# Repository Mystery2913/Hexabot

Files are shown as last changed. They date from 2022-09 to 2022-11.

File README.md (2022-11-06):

# Hexabot - A hexapedal robot from scratch


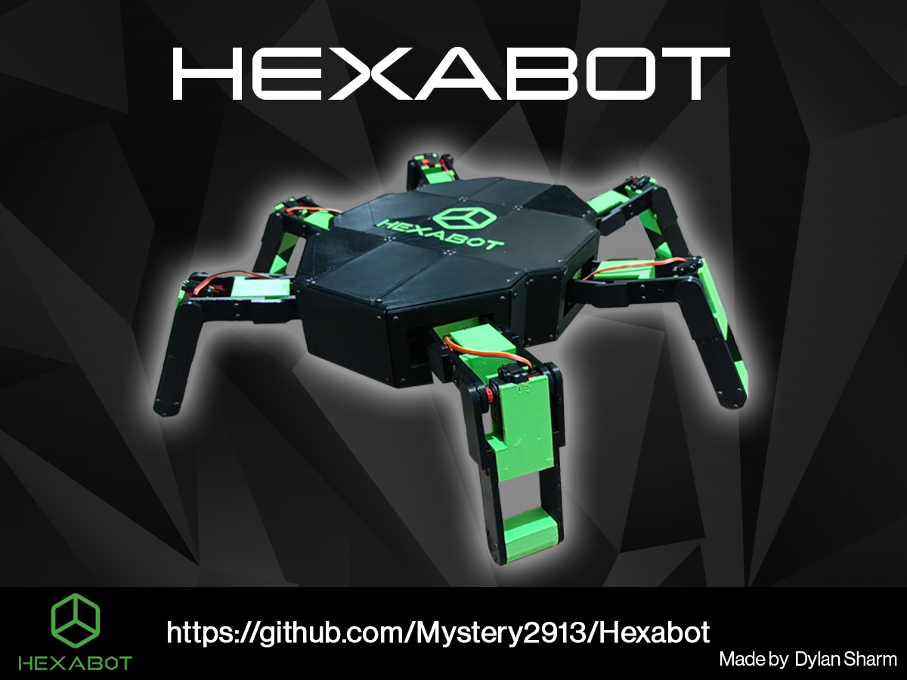
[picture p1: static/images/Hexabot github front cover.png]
Front Cover Image of Hexabot


## Introduction
Author: **Dylan Sharm**

**Hexabot** is a fully developed hexapedal robot made using 3D printing. Comprising of a 3D printed body, it contains the leg mechanisms for 3 joints to move each leg in 3 dimensions. All 6 legs allow for a stable base for walking around. The system is controlled by a local website run on a Raspberry Pi 4, while control system features speed control and standing control. The robot is powered by a 7.4v 7500mAh battery that is removable from the robot with power indicator light included.

## Building Hexabot
To build Hexabot, follow the **[user manual](Hexabot_User_Manual.pdf)**. It details all instructions of how to make Hexabot including components and tools, materials, assembly instructions and diagrams, software instructions, supporting tips, and safety information. Using this, a fully contracted Hexabot can be made.

## Hexabot Software Installation
Install Raspberry Pi OS onto raspberry pi. After installation, enable I2C and SSH in `Preferences > Raspberry Pi Configuration`

Install `git` onto system:
```
sudo apt update
sudo apt install git
```
Verify the installation. Should return lasted version (2.32.0):
```
git --version
```
Then after installation and configuration, navigate to Projects in users:
```
cd Projects
```
Clone repository:
```
git clone https://github.com/Mystery2913/Hexabot.git
```
Navigate into repo:
```
cd Hexabot
```
Install dependencies:
```
pip install -r requirements.txt
```
Startup Control site
```
flask run --no-debugger --host=0.0.0.0
```
Use addresses printed in console to connect to website, and add /joy to address to access control panel.

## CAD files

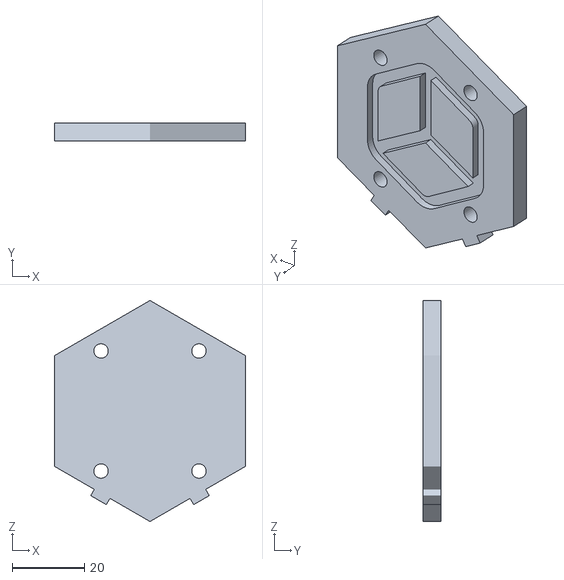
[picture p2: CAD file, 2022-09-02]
STL files/Battery Housing/BH-3.stl
53.0 x 5.00 x 61.2

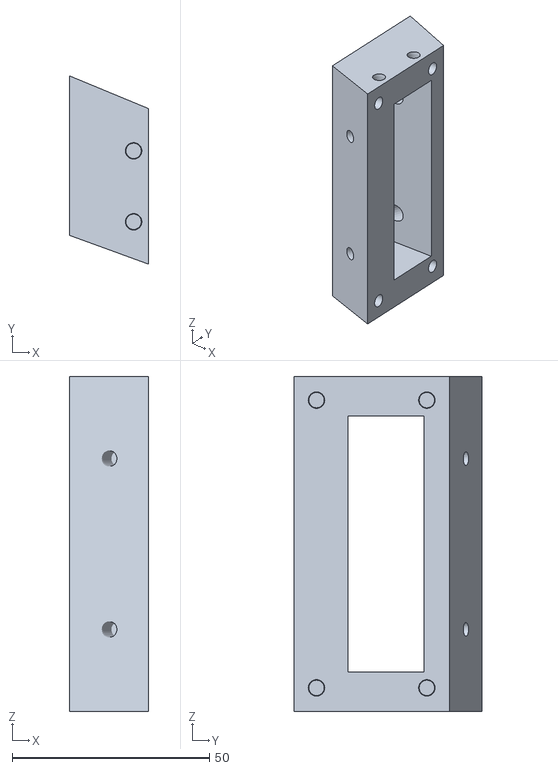
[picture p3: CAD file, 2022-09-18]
STL files/Body Frame/External Plates/BF-EP-3.stl
20.0 x 47.7 x 85.0

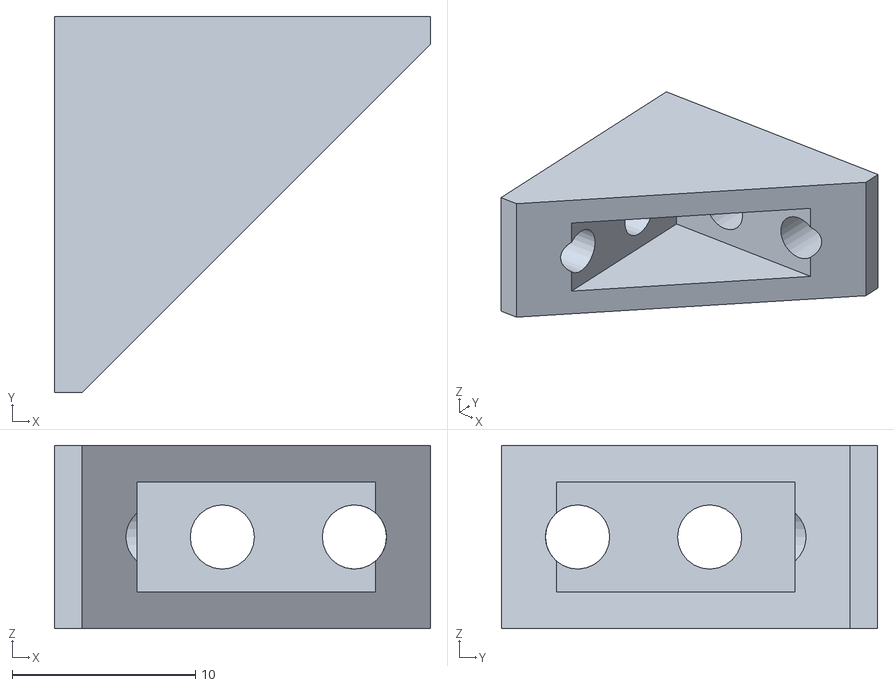
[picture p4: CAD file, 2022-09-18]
STL files/Body Frame/Internal Frame/BF-IF-B.stl
20.5 x 20.5 x 10.0

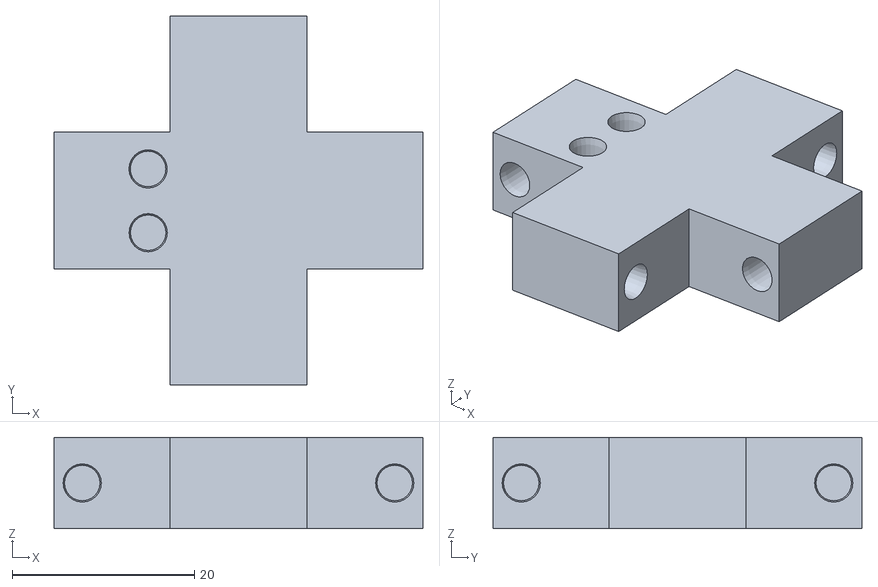
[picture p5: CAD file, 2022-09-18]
STL files/Body Frame/Internal Frame/Bottom Frame/BF-IF-BF-S-11.stl
40.5 x 40.5 x 10.0

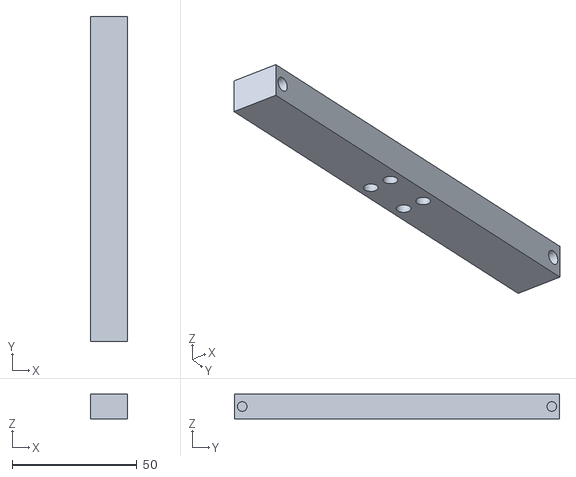
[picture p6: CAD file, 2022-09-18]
STL files/Body Frame/Internal Frame/Top Frame/BF-IF-TF-S-8.stl
15.0 x 130.3 x 10.0

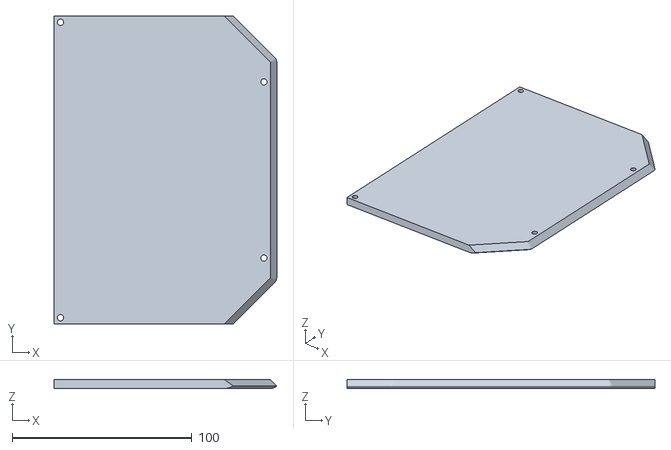
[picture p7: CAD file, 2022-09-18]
STL files/Detachable Plates/External Plates/Bottom Plates/DP-EP-BP-6.stl
123.8 x 171.3 x 5.00

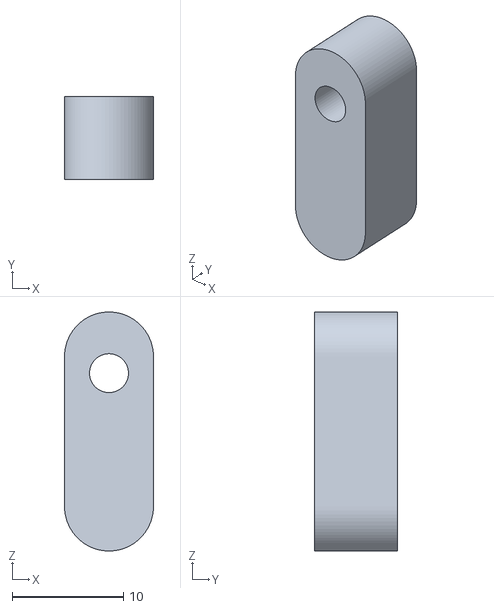
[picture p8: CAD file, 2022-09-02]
STL files/Detachable Plates/External Plates/DP-BC.stl
8.00 x 7.50 x 21.5

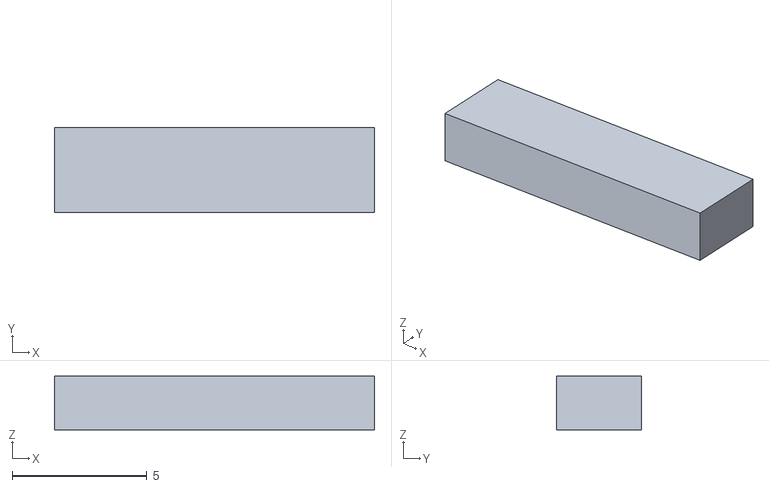
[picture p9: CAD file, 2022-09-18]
STL files/Detachable Plates/External Plates/Logo Plates/DP-EP-LP-5.stl
11.9 x 3.15 x 2.00

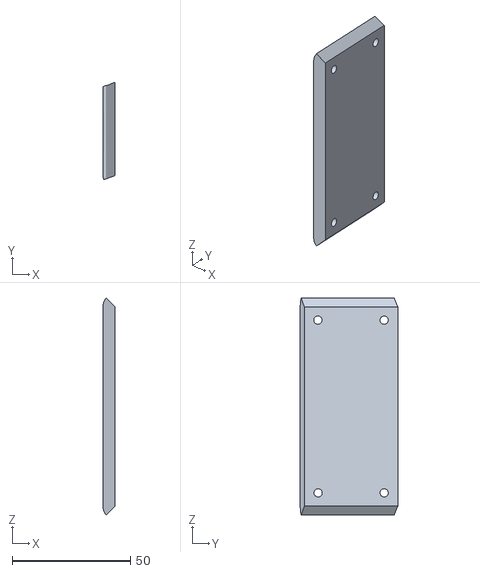
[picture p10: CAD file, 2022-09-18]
STL files/Detachable Plates/External Plates/Outer Plates/DP-EP-OP-15.stl
5.00 x 41.2 x 91.7

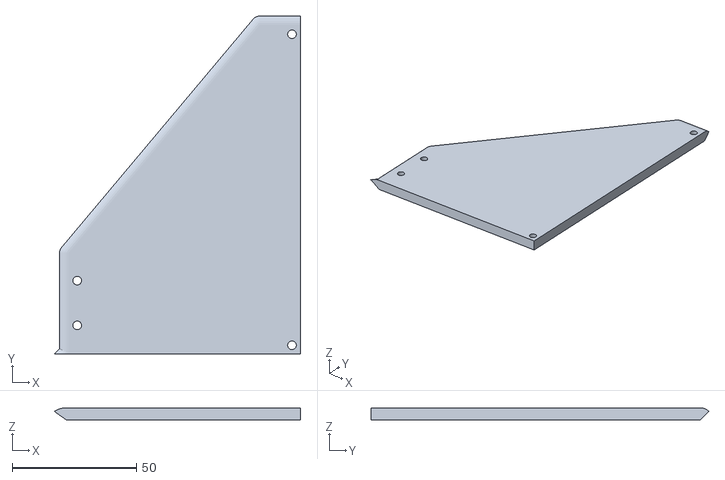
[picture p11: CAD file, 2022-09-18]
STL files/Detachable Plates/External Plates/Top Plates/DP-EP-TP-1.stl
99.2 x 136.1 x 5.00

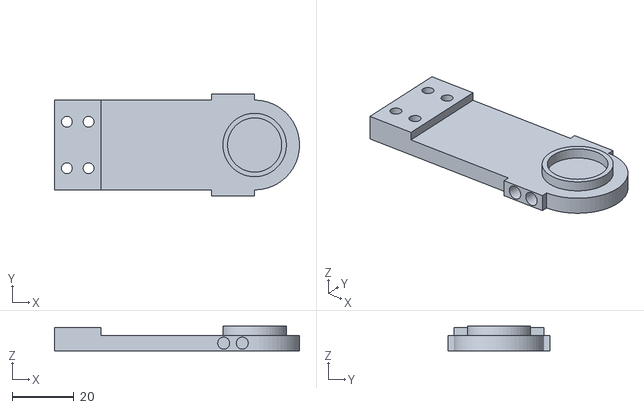
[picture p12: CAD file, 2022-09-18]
STL files/Motion System/Leg Connector/MS-LC-1.stl
79.1 x 33.0 x 8.00

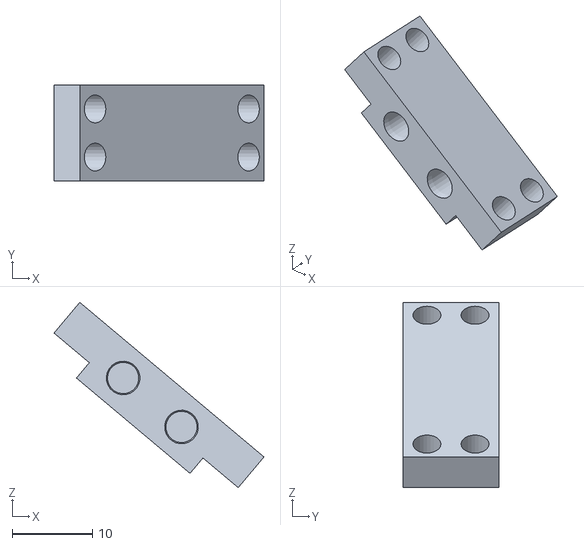
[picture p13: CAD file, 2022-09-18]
STL files/Motion System/Leg/MS-L-9.stl
26.2 x 12.0 x 23.1

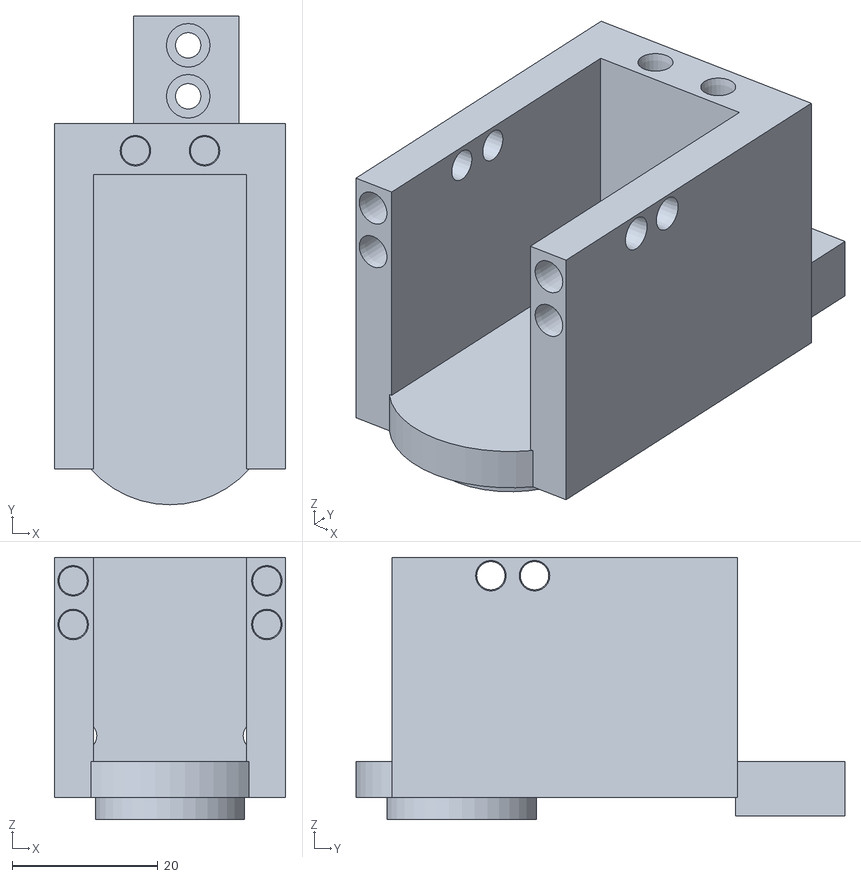
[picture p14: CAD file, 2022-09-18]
STL files/Robot main/RM-MS-7.stl
31.8 x 67.1 x 36.0

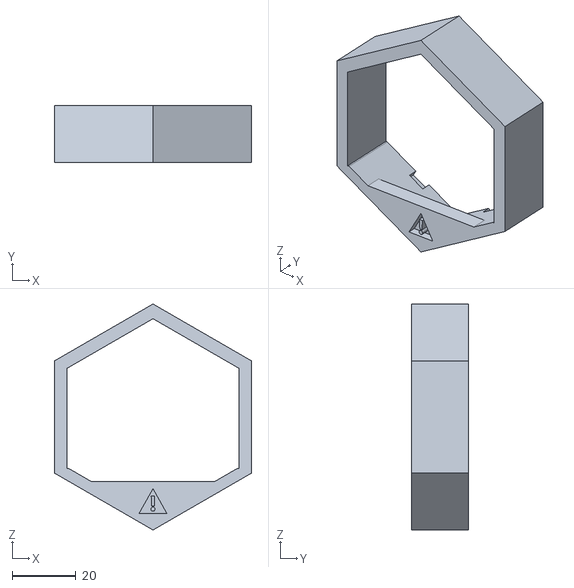
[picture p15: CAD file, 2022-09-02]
STL files/Battery Housing/BH-5.stl
62.0 x 18.0 x 71.0

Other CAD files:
STL files/Body Frame/External Plates/BF-EP-6.stl
STL files/Body Frame/Internal Frame/Bottom Frame/BF-IF-BF-S-1.stl
STL files/Body Frame/Internal Frame/Top Frame/BF-IF-TF-S-15.stl
STL files/Detachable Plates/External Plates/Bottom Plates/DP-EP-BP-1.stl
STL files/Battery Housing/BH-1.stl
STL files/Battery Housing/BH-2.stl
STL files/Battery Housing/BH-4.stl
STL files/Body Frame/External Plates/BF-EP-1.stl
STL files/Body Frame/External Plates/BF-EP-10.stl
STL files/Body Frame/External Plates/BF-EP-11.stl
STL files/Body Frame/External Plates/BF-EP-12.stl
STL files/Body Frame/External Plates/BF-EP-13.stl
STL files/Body Frame/External Plates/BF-EP-14.stl
STL files/Body Frame/External Plates/BF-EP-15.stl
STL files/Body Frame/External Plates/BF-EP-16.stl
STL files/Body Frame/External Plates/BF-EP-2.stl
STL files/Body Frame/External Plates/BF-EP-4.stl
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

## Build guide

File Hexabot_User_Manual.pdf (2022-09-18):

Hexabot Handbook – V1.0.0

## Table of Content

## 1 Introduction

Thank you for taking the time to look at this project and consider building it. I have worked many hours to refine this design so that it is easy to assemble by 3D printer, and that it builds skills of 3D printing, electronics, and software development. This manual will instruct you how to build your own Hexabot, and how to troubleshoot any problems that present themselves along the way.

### 1.1 Safety Disclaimer

The building of this robot will require the use of techniques and tools which when used incorrectly could result in physical harm. When using these tools, please take the time to follow the safety instructions listed with each tool and technique. Overall personal protection equipment (PPE) should be used when using most tools.

### 1.2 Symbols

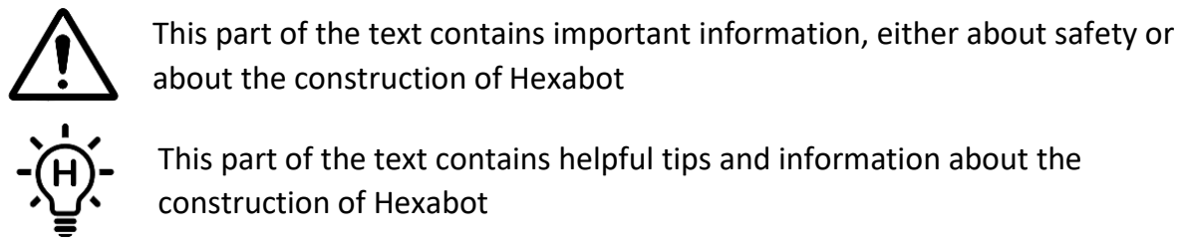
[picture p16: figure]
about the construction of Hexabot; construction of Hexabot

## 2 Overview

Hexabot is hexapedal 3D printed robot that is designed to walk around in developed areas to gather data and to scout the area. At the current time, the data collection feature is still being developed, and will be implemented in the future. The rigid design allows the robot to be sturdy, and also to be able to carry heavy loads on its back. Each of the 6 legs has 3 servo motors: two for the X and Y axis, and one for Z axis. Each leg’s motors are connected to a breakout board that connects each motor to power and signal. The signal wires of the motors are connected to 2 Adafruit 16-Channel I2C Servo Driver called the PCA9685. This board controls the PWM signal for the motors and allows the motors to be controlled by the brains of the robot: a Raspberry Pi 4. The robot is powered by a 7500mAh LiPo battery that is connected by a slot-in battery design that allows for easy connection of the battery. The link to repository to make Hexabot is here: https://github.com/Mystery2913/Hexabot

This part of the text contains important information, either about safety or

This part of the text contains helpful tips and information about the

## 3 Components and Tools List

This robot requires multiple tools and components to fully construct it. Most of the components for the body are 3D printed, a lot of the functional components that drives Hexabot are not.

### 3.1 Components

This list contains all the components and their quantities required to build Hexabot. The links provided are where I purchased the supplies, however the same or similar products from different supplies are also satisfactory. Just make sure that their dimensions are the same, as they may not be compatible with the 3D prints.

3.1.1 Threaded inserts

Purchase link: https://nz.rs-online.com/web/p/threaded-inserts/2040616/

Quantity: 800

Notes: 800 is enough to assemble Hexabot, however if any mistakes are made and some parts are needed to be remade, more will be required.

3.1.2 Screws

Purchase link: https://nz.rs-online.com/web/p/socket-screws/0281192/

Quantity: 800

3.1.3 Servos

Purchase link: https://nz.banggood.com/URUAV-URS001-180-20KG-Digital-Metal-Gear-Servo-Waterproof-CNC-For-RC-Car-Models-or-Quadcopter-or-Helicopter-or-Robot-or-Intelligent-Robot-Arm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 (https://nz.banggood.com/URUAV-URS001-180-20KG-Digital-Metal-Gear-Servo-Waterproof-CNC-For-RC-Car-Models-or-Quadcopter-or-Helicopter-or-Robot-or-Intelligent-Ro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)

Quantity: 18

3.1.4 Servo Drivers

Purchase link: https://learningdevelopments.co.nz/products/adafruit-16-channel-12-bit-pwm-servodriver-i2c-interface (https://learningdevelopments.co.nz/products/adafruit-16-channel-12-bit-pwm-servo-driver-i2c-interface)

Quantity: 2

3.1.5 Raspberry Pi 4 and SD card

Purchase link: https://www.pbtech.co.nz/product/SEVRBP0206/Raspberry-Pi-4-Model-B-4GB-LPDDR4-FIRST-28nm-Based (https://www.pbtech.co.nz/product/SEVRBP0206/Raspberry-Pi-4-Model-B-4GB-LPDDR4-FIRST-28nm-Based)

Quantity: 1

Notes: The purchase link has a 4GB model attached to it, but a 2GB or 8GB model will also be sufficient.

Purchase link: h https://www.pbtech.co.nz/product/MEMKIC11132/Kingston-High-Endurance-32GBmicroSDHC-CL10-UHS-I (https://www.pbtech.co.nz/product/MEMKIC11132/Kingston-High-Endurance-32GB-microSDHC-CL10-UHS-I)

Quantity: 1

3.1.6 Power switch

Purchase link: https://www.jaycar.co.nz/spst-mini-rocker-switch/p/SK0984

Quantity: 1

3.1.7 Wires

Purchase link: https://www.jaycar.co.nz/8-gauge-figure-8-power-cable-sold-per-metre/p/WH3063

Quantity: 1m

Purchase link: https://www.jaycar.co.nz/25a-2-core-tinned-dc-power-cable-sold-permetre/p/WH3087 (https://www.jaycar.co.nz/25a-2-core-tinned-dc-power-cable-sold-per-metre/p/WH3087)

Quantity: 2m

Purchase link: https://www.jaycar.co.nz/150mm-socket-to-socket-jumper-leads-40-piece/p/WC6026

Quantity: 1 pack of 40

3.1.8 Wire crimps large/small

Purchase link: https://www.jaycar.co.nz/red-black-gold-crimp-cable-small-eye-terminals-pk-2/p/PT4560 (https://www.jaycar.co.nz/red-black-gold-crimp-cable-small-eye-terminals-pk-2/p/PT4560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)

Quantity: 2 sets of 2

Purchase link: https://www.jaycar.co.nz/eye-terminal-red-pk-100/p/PT4515

Quantity: 100

Notes: 100 will not be needed, but it is good to have so spare.

3.1.9 Power screws and bolts

Purchase link: https://www.mitre10.co.nz/shop/hillman-machine-screws-m5-x-40mm-pack-of-6-zinc-plated/p/325944 (https://www.mitre10.co.nz/shop/hillman-machine-screws-m5-x-40mm-pack-of-6-zinc-plated/p/325944)

Quantity: 1 pack of 6

Purchase link: https://www.mitre10.co.nz/shop/hillman-machine-screws-m5-x-10mm-zinc-plated/p/325938 (https://www.mitre10.co.nz/shop/hillman-machine-screws-m5-x-10mm-zinc-plated/p/325938)

Quantity: 2 pack of 8

Purchase link: https://www.mitre10.co.nz/shop/bremick-hex-nuts-m5/p/349125

Quantity: 20

3.1.10 PCB and header pins

Purchase link: https://jlcpcb.com/

Quantity: 10

Notes: I used JLCPCB for my PCBs, however other companies are also good. To order them, upload the PCB .gerber file found in GitHub repo to the website and order 10 PCBs with default settings but with an outer copper weight of 2 oz.

Purchase link: https://www.jaycar.co.nz/40-pin-header-terminal-strip/p/HM3212

Quantity: 2 sets of 40

Notes: These are used for the wire connection to the PCBs, and the spares pins are used for the power indicator circuit.

3.1.11 Battery

Purchase link: https://hobbystation.co.nz/giant-power-graphene-2s-7-4v-7500mah-100c-hardcase-lipo-w-bullet-to-t-plug/ (https://hobbystation.co.nz/giant-power-graphene-2s-7-4v-7500mah-100c-hardcase-li-po-w-bullet-to-t-plug/)

Quantity: 1

3.1.12 Metal plates

Purchase link: https://www.jaycar.co.nz/rare-earth-magnet-small-pk-4/p/LM1622

Quantity: 1

Notes: I used the piece of metal that these magnets came with since it was the right dimensions and material for the battery plates. However other nickel-plated steel will work with the right dimensions.

3.1.13 Spring

Purchase link: https://nz.rs-online.com/web/p/compression-springs/0821245/

Quantity: 1

3.1.14 JST-XH connector

Purchase link: https://www.jaycar.co.nz/connectors-kit-with-popular-jst-xhp-and-ph2-headers/p/PT4457 (https://www.jaycar.co.nz/connectors-kit-with-popular-jst-xhp-and-ph2-headers/p/PT4457)

Quantity: 1

Notes: This kit has the connectors and headers to wire up the charging port.

3.1.15 Heat shrink tubing

Purchase link: https://www.mitre10.co.nz/shop/swordfish-heat-shrink-assortment-127-piece/p/228818 (https://www.mitre10.co.nz/shop/swordfish-heat-shrink-assortment-127-piece/p/228818)

Quantity: 1

Notes: This kit has heat shrink tubing for all posable wire in this project. A heat source is also needed for them, e.g., lighter, matches.

3.1.16 Power indicator circuit

The power indictor circuit is made on a perfboard using hand soldering and THT (through hole technology) components.

3.1.16.1 Perfboard

Purchase link: https://www.jaycar.co.nz/connectors-kit-with-popular-jst-xhp-and-ph2-headers/p/PT4457 (https://www.jaycar.co.nz/connectors-kit-with-popular-jst-xhp-and-ph2-headers/p/PT4457)

Quantity: 1

Notes: This kit has the connectors and headers to wire up the charging port.

3.1.16.2 Resistors

Purchase link: https://www.jaycar.co.nz/680-ohm-1-watt-carbon-film-resistors-pack-of-2/p/RR2770

Quantity: 1 set of 2

Purchase link: https://www.jaycar.co.nz/330-ohm-1-watt-carbon-film-resistors-pack-of-2/p/RR2762

Quantity: 1 set of 2

3.1.16.3 Transistors

Purchase link: https://www.jaycar.co.nz/2n2222a-npn-transistor/p/ZT2298

Quantity: 2

3.1.16.4 RGB LED

Purchase link: https://www.jaycar.co.nz/tricolour-rgb-5mm-led-600-1000mcd-rounddiffused/p/ZD0270 (https://www.jaycar.co.nz/tricolour-rgb-5mm-led-600-1000mcd-round-diffused/p/ZD0270)

Quantity: 1

3.1.17 Battery Spring Contacts

Purchase link: https://nz.rs-online.com/web/p/battery-contacts/1094719/

Quantity: 1 bag of 10

3.1.17 Raspberry pi battery pack and cable

Purchase link: https://www.jaycar.co.nz/power-pack-for-raspberry-pi-with-li-ion-battery/p/XC9060

Quantity: 1

Purchase link: https://www.jaycar.co.nz/usb-type-c-to-usb-3-0-a-male-cable/p/WC7758

Quantity: 1

### 3.2 Tools

3.2.1 Soldering iron, soldering tip, and solder

Purchase link: https://www.jaycar.co.nz/duratech-48w-temperature-controlled-solderingstation/p/TS1620 (https://www.jaycar.co.nz/duratech-48w-temperature-controlled-soldering-station/p/TS1620)

Quantity: 1

Purchase link: https://www.jaycar.co.nz/conical-0-5mm-soldering-iron-tip/p/TS1622

Quantity: 1

Purchase link: https://www.jaycar.co.nz/0-71mm-duratech-solder-200gm/p/NS3005

Quantity: 1

Note: This solder is lead-based and therefore is not RoHS (Restriction of Hazardous Substances) compliant. Lead free solder will work the same for this application so it is based on personal preference.

3.2.2 Screw drivers set

Purchase link: https://www.mitre10.co.nz/shop/number-8-precision-bits-set-23-pieces-black-andorange/p/343370 (https://www.mitre10.co.nz/shop/number-8-precision-bits-set-23-pieces-black-and-orange/p/343370)

Quantity: 1

3.2.3 Electric screwdriver

Purchase link: https://www.banggood.com/Wowstick-1F+-64-In-1-Cordless-Electric-Screwdriver-Lithium-ion-Charge-LED-Power-Screwdriver-p-1294707.html (https://www.banggood.com/Wowstick-1F+-64-In-1-Cordless-Electric-Screwdriver-Lithium-ion-Charge-LED-Power-Screwdriver-p-1294707.html)

Quantity: 1

Notes: This electric screwdriver has a good balance between price and quality and has worked well for its purpose during my time of using it. However, did have an issue with the charging port stopping charging. To Banggood’s credit, they did send me a replacement. Purchase at own discretion.

3.2.4 Scraper

Purchase link: https://www.mitre10.co.nz/shop/number-8-paint-scraper-38mm/p/286933

Quantity: 1

Notes: Most 3D printers come with a scraper for removing prints from the heated bed, which can be used instead.

3.2.5 Wire crimper/stripper

Purchase link: https://www.jaycar.co.nz/heavy-duty-wire-stripper-cutter-crimper-with-wireguide/p/TH1827 (https://www.jaycar.co.nz/heavy-duty-wire-stripper-cutter-crimper-with-wire-guide/p/TH1827)

Quantity: 1

3.2.6 Tweezers

Purchase link: https://www.jaycar.co.nz/anti-magnetic-precision-tweezers/p/TH1754

Quantity: 1

3.2.7 Needle nose pliers

Purchase link: https://www.jaycar.co.nz/precision-6-long-nose-pliers/p/TH1887

Quantity: 1

3.2.8 Helping hand

Purchase link: https://www.jaycar.co.nz/third-hand-pcb-holder-tool-with-2-clips-and-heavybase/p/TH1982 (https://www.jaycar.co.nz/third-hand-pcb-holder-tool-with-2-clips-and-heavy-base/p/TH1982)

Quantity: 1

3.2.9 File set

Purchase link: https://www.mitre10.co.nz/shop/jobmate-file-set-10-piece-black/orange/p/367947

Quantity: 1

3.2.10 Clippers

Purchase link: https://www.jaycar.co.nz/precision-127mm-angled-side-cutters/p/TH1897

Quantity: 1

3.2.11 Battery charger

Purchase link: https://hobbystation.co.nz/gt-power-battery-charger-b3-lipo-1amp-2-3cell-240v/

Quantity: 1

3.2.12 Glue gun and glue

Purchase link: https://www.jaycar.co.nz/mini-glue-gun/p/TH1997

Quantity: 1

Purchase link: https://www.jaycar.co.nz/7mm-glue-sticks-for-mini-gun-pack-of-6/p/TH1991

Quantity: 1 pack of 6

3.2.13 Drill and bits

Purchase link: https://www.mitre10.co.nz/shop/black-decker-drill-driver-kit-18-volt/p/348328

Quantity: 1

Purchase link: https://www.mitre10.co.nz/shop/number-8-drill-bit-set-19-piece/p/277294

Quantity: 1

Purchase link: https://www.mitre10.co.nz/shop/bosch-metal-drill-bit-5-5mm-silver/p/278417

Quantity: 1

3.2.14 8mm spanner

Purchase link: https://www.mitre10.co.nz/shop/fuller-pro-spanner-ring-and-open-end-8mm/p/254065 (https://www.mitre10.co.nz/shop/fuller-pro-spanner-ring-and-open-end-8mm/p/254065)

Quantity: 1

### 3.3 Safety instructions

The tools and instruments used in the assembly of this robot are hazardous and have safety risks involved in their use. Foremostly, many of them have hot temperature areas that can cause serious damage to your person. As well as the risk to personal health, there is the risk of leaving a tool on and causing a house fire. When finishing with a tool, make sure it is turned off and in a safe place.

## 4 3D Printing

The most important tool in the making of Hexabot is a 3D printer. The main body and walking mechanism of Hexabot is 3D printed, the quality of the parts is paramount to the quality of the final result.

### 4.1 3D Printer

The 3D printer I used is Creality’s Ender 5 Pro. I purchased mine from Kiwi3D, (https://kiwi3d.co.nz/product/creality3d-ender-5-pro/) and I have only got amazing service from them, I can highly recommend. It is priced at around $650 NZD and is more of an intermediate level printer. However, all the parts are printable on an entry level 3D printer as long as it has a minimum print volume of 140x140x130mm which is pretty standard. If the printer volume is less than this, adjustments can be made so that it all works out. For the prints, I highly recommended upgrading the default nozzle of 0.4mm to a 0.6mm nozzle. This will half the print times and the lost resolution will not affect the printed parts. This 0.6mm stainless steel nozzle (https://kiwi3d.co.nz/product/0-6mm-stainless-steel-m6-nozzle/) from Kiwi3D has worked well for me. The only other modification that I can recommend is the use of octoprint. Octoprint is a printer management software that is installed on a raspberry pi and is connected to the printer. It allows full control of the printer from anywhere on the local network and has a thriving community of developers making amazing extension for the software. For more information on how to do that, visit All3DP. (https://all3dp.com/2/octoprint-setup-how-to-install-octopi-on-a-raspberry-pi/)

### 4.2 3D Filament

For the making of Hexabot, a lot of high-quality plastics is needed. PLA is a great polymer that is cost effective, easy to 3D print, and is in ready supply. I get all my filament form Kiwi3D, as they have good prices, a wide range, and most importantly they are based in New Zealand. In my version, I use black and green as my main 2 colours, however any colour can be used. The only important characteristics to look for when buying other filaments is the 1.75mm diameter and print temperature in the range of 190-220°C.

Black PLA

Purchase link: https://kiwi3d.co.nz/product/kiwi3d-black-pla-3kg/

Quantity: 2 spools of 3kg

Notes: Black is used for the main prints of Hexabot. If the colour of the part is not specified, then use black PLA.

Green PLA

Purchase link: https://kiwi3d.co.nz/product/kiwi3d-green-pla/

Quantity: 1 spool of 1kg

Notes: Green is used for the highlights of Hexabot. When green is required, it will be specified in the assembly requirements.

### 4.3 Printer settings

The settings that a printer uses are very important for obtaining high quality prints and ensuring the effectiveness of the device. This process of finding the best settings for a printer is a tedious one, however it is vital for making good prints. I have exported my specific settings that I used to print the parts in the GitHub repository. These settings will not work for all printers, however their key principles will. Here are the most important settings for printing these parts with a 0.6mm nozzle:

Layer height: 0.4mm

Line width: 0.6mm

Wall thickness: 1.2mm

Wall count: 2

Top/Bottom thickness: 1.6mm

Top/Bottom layer count: 3

Infill density: 20%

> Note: This value may change depending on the print, which will be noted in its required section.

Infill pattern: Grid

> Note: This setting is personal preference, and because it runs nicely on my printer. Other patterns will be suitable.

Printing Temperature: 230°C

> Note: This temperature is required because of the larger nozzle. If the filament is too ‘runny’ lower the print temperature incrementally until the issue goes away.

Build Plate Temperature: 60°C

Print Speed: 50mm/s

> Note: This value is dependent on the stability of the printer and the power of the hotend. This value should be as high as possible while keep good print quality.

## 5 Part preparation instructions

During assembly, many parts will require preparation before they are able to be installed. These range from when they are of the print bed, to just before they are in their final place.

### 5.1 3D parts naming scheme

Because of the large number of parts, and therefore files that are needed to construct Hexabot, there is a naming scheme such that all the files are organised. There are 5 main groups where there installs will be at the start of the file name. These 5 groups are: battery housing, body frame, detachable plates, motion system, and robot main. All of the STL files will be sorted into folders in these 5 groups, as well as other distinctions made below:

RM = Robot Main | BF = Body Frame | EP = External Plates | IF = Internal Frame
BF = Bottom Frame | TF = Top Frame | S = Strut | B = Bracket
DP = Detachable Plates TP = Top Plates | BP = Bottom Plates | OP = Outer Plates
BC = Battery Clasp | BH = Battery Housing MS = Motion System | LC = Leg Connector
L = Leg | LP = Logo Plates | EM= Electronics mount

These file codes will be used to refer to parts during the assembly process. For example the first part in the top frame of body frame has the code BF-IF-TF-S-1. This is for body frame, internal frame, top frame, strut.

### 5.2 Preparing off the print bed

After a print has finished, there a few things that need to be prepared before threaded inserts can be installed. Firstly, some prints need supports to be printed and then subsequently removed. To do this pulling them off by hand will mostly do, however in some cases, using the scraper can speed the task up. Secondly, after the print has finished, there can be some minor errors on print that need to be removed (e.g. stringing). To remove these, use a file and grind off these imperfections.

### 5.3 Drilling holes and inserting brass threads

After the printed parts have been initially prepared, the holes in the parts need to be drilled because of the expansion that print causes. Before doing this, check using one of the screws if it can fit through directly off the print. If it can, the drilling step is not necessary. Use a 3.5mm drill bit and widen the holes in the prints. This step for all prints is only an issue if the printer over extrudes on wall layers. When drilling out the holes, make sure that the holes go all the way through the parts, since otherwise it could be meant for a hole with brass thread. After drilling is finished, the brass threaded inserts need to be installed. The brass threads are inserted into the small holes about 4mm wide and 7mm deep (see Figure 1). To do this follow the steps below:

1. Turn on soldering iron to highest temperature setting.
2. Prepare 3D part by having it with the holes facing upwards and having the brass thread and a pair of tweezers nearby.
3. Once the soldering iron has headed up, use the tweezers to place bottom (smaller diameter section) of the threaded insert into the hole. Then place the tip of the soldering iron into the opening of the threaded insert and start to apply downward pressure (see Figure 1).
4. Just before the threaded insert is flush with the part, use the tweezers to stop pushing in the part and return the soldering iron to its holder (see Figure 2).
5. Take the scraper and use to make sure the threaded insert is flush with the part by pushing the threaded insert down the rest of the way (see Figure 3).

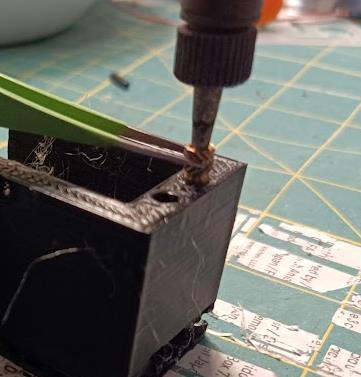
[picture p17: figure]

Figure 1

How to start inserting the brass thread.

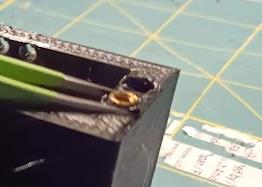
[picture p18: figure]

Figure 2

Stopping the threaded insert from being completely flush.

Figure 3

Making the threaded insert flush with the scraper.

## 6 Top frame assembly

### 6.1 Required parts and tools

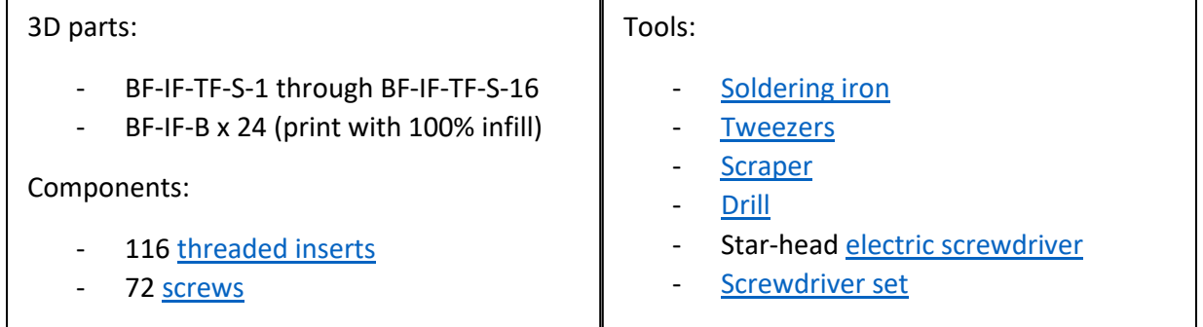
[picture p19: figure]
3D parts:; - BF-IF-TF-S-1 through BF-IF-TF-S-16 - BF-IF-B x 24 (print with 100% infill); Components:; - 116 threaded inserts - 72 screws; Tools:; - Soldering iron - Tweezers - Scraper - Drill - Star-head electric screwdriver - Screwdriver set

### 6.2 Preparing parts

Prepare parts as instructed in section 5.2 and 5.3. In this part there are some threaded inserts that will not be used immediately, as they will be used at a later date. The only ones that will be needed are ones used in the assembly diagram.

### 6.3 Assembly

Layout frame as seen in diagram below (Figure 4). Use screws in conjunction with the angled brackets (BF-IF-B) to connect all the frame together. The brackets at ends of the frames will only be partially attached.

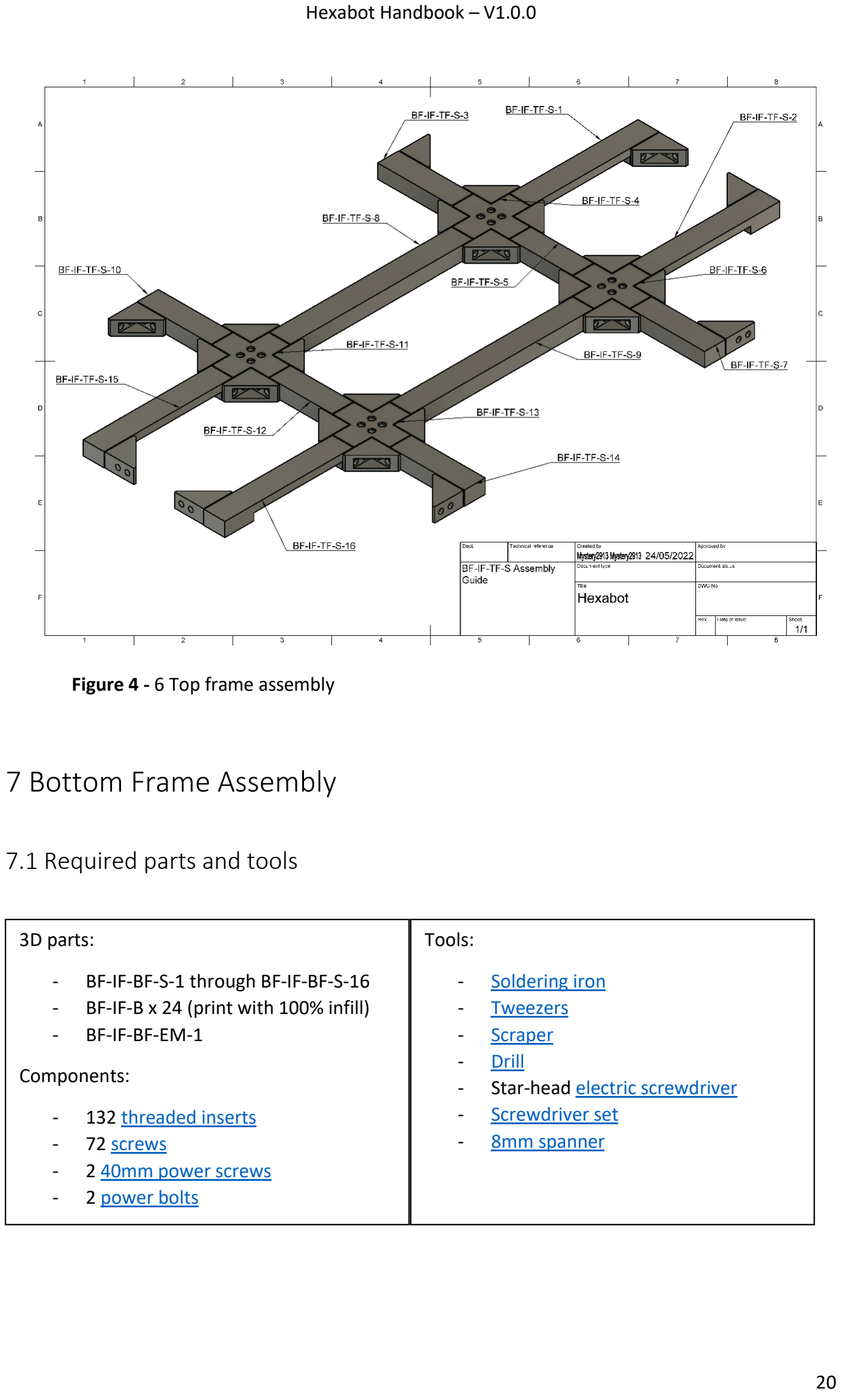
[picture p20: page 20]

Figure 4 - 6 Top frame assembly

## 7 Bottom Frame Assembly

### 7.1 Required parts and tools

3D parts:

- BF-IF-BF-S-1 through BF-IF-BF-S-16
- BF-IF-B x 24 (print with 100% infill)
- BF-IF-BF-EM-1

Components:

- 132 threaded inserts
- 72 screws
- 2 40mm power screws
- 2 power bolts

Tools:

- Soldering iron
- Tweezers
- Scraper
- Drill
- Star-head electric screwdriver
- Screwdriver set
- 8mm spanner

### 7.2 Preparing parts

Prepare parts as instructed in section 5.2 and 5.3. In this part there are some threaded inserts that will not be used immediately, as they will be used at a later date.

### 7.3 Assembly

Layout frame as seen in diagram below (Figure 5). Use screws in conjunction with the angled brackets (BF-IF-B) to connect all the frame together. The brackets at ends of the frames will only be partially attached. To install power screws, slot the screws into the 5mm holes in parts BF-IF-BF-S-8 and BF-IF-BF-S-9. Then use the power bolt to attach them to the parts using the 8mm spanner.

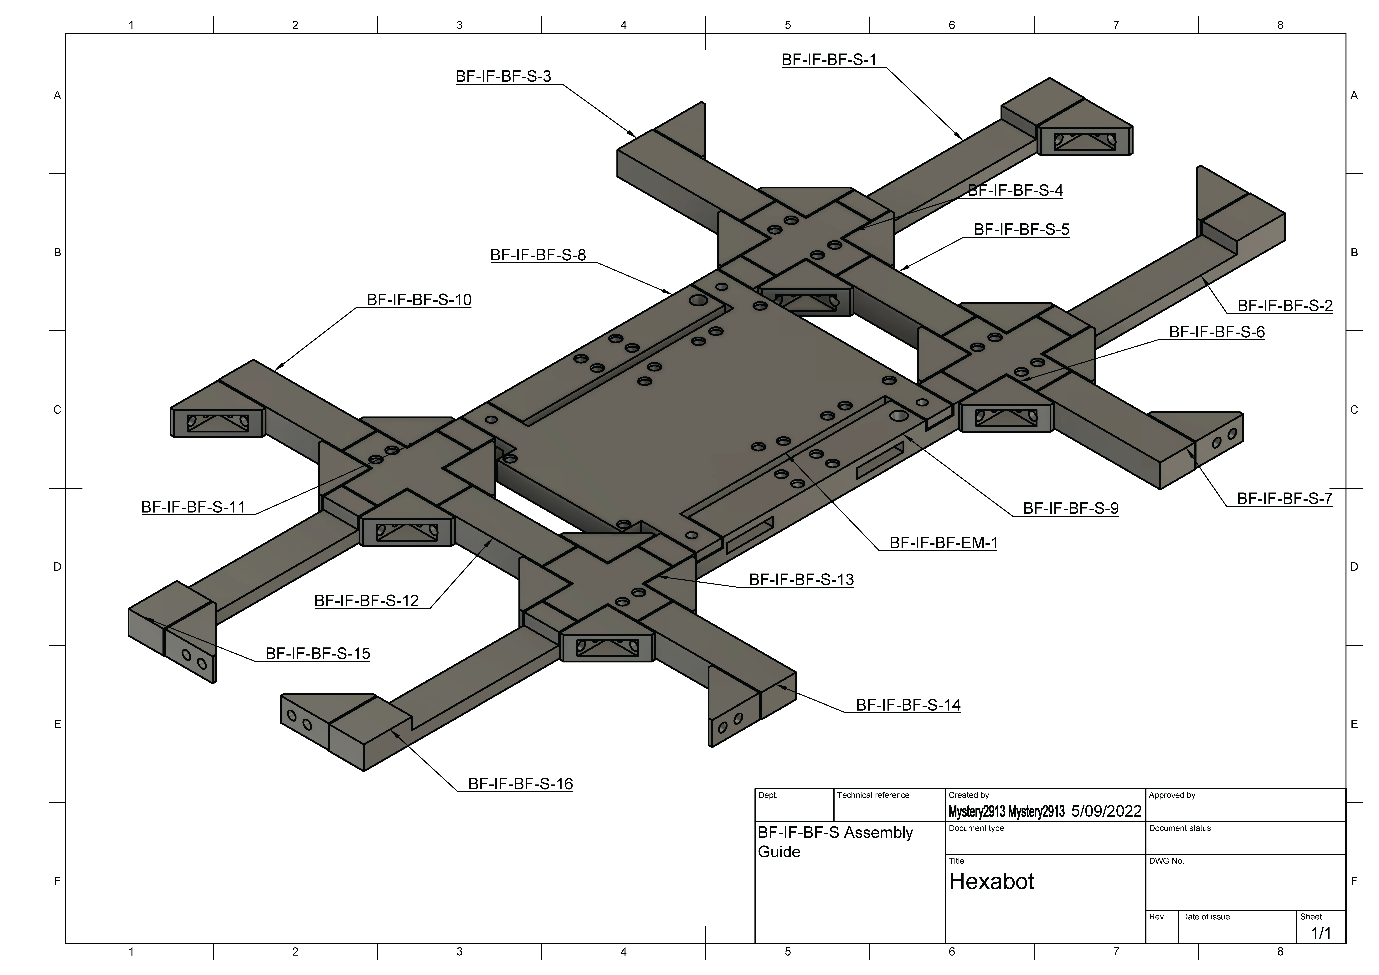
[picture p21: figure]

Figure 5 – 7 Bottom frame assembly

## 8 External Frame Assembly

### 8.1 Required parts and tools

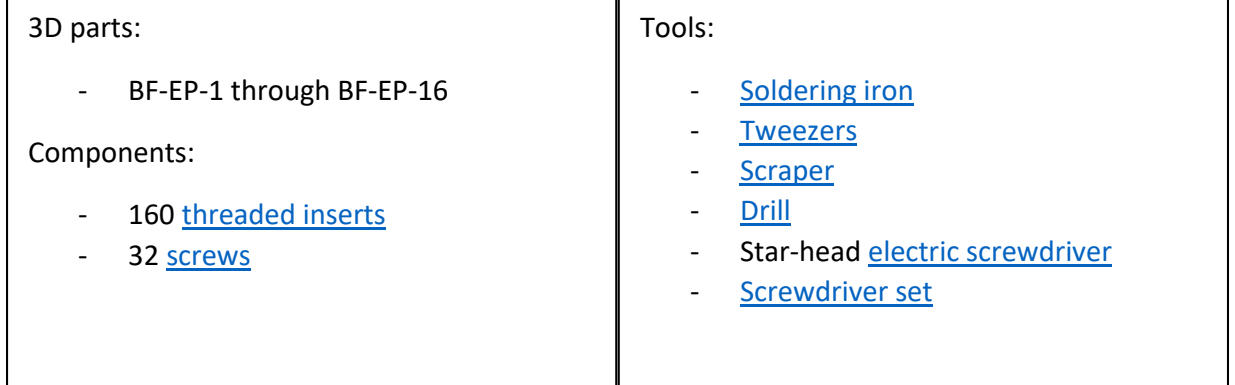
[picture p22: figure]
3D parts:; - BF-EP-1 through BF-EP-16; Components:; - 160 threaded inserts - 32 screws; Tools:; - Soldering iron - Tweezers - Scraper - Drill - Star-head electric screwdriver - Screwdriver set

### 8.2 Preparing parts

Prepare parts as instructed in section 5.2 and 5.3. In these parts there are screw holes that have openings for the heads to be ‘submerged’ in the plastic. Because of this there are some holes that may need to be widened with a larger drill bit. When doing this, use a 6mm drill bit.

### 8.3 Assembly

To assemble, insert the screws in the two holes in the side of each piece. Do this around the whole part so that it connects together in an enclosed loop and is held strong.

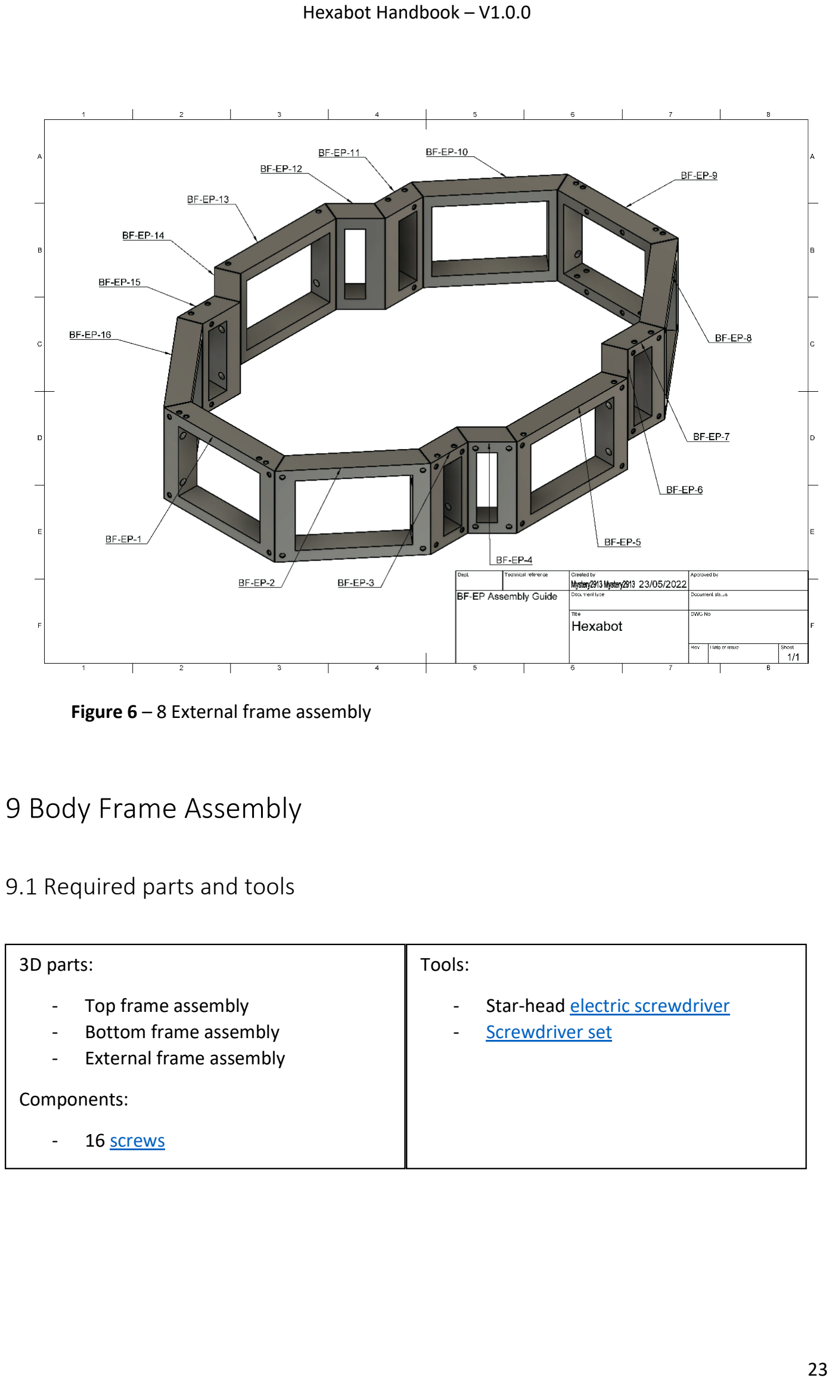
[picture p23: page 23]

Figure 6 – 8 External frame assembly

## 9 Body Frame Assembly

### 9.1 Required parts and tools

3D parts:

- Top frame assembly
- Bottom frame assembly
- External frame assembly

Components:

- 16 screws

Tools:

- Star-head electric screwdriver
- Screwdriver set

### 9.2 Assembly

To connect these 3 sections together, use screws in the angled brackets at the ends of the top and bottom frame assembly and connect them to the external frame.

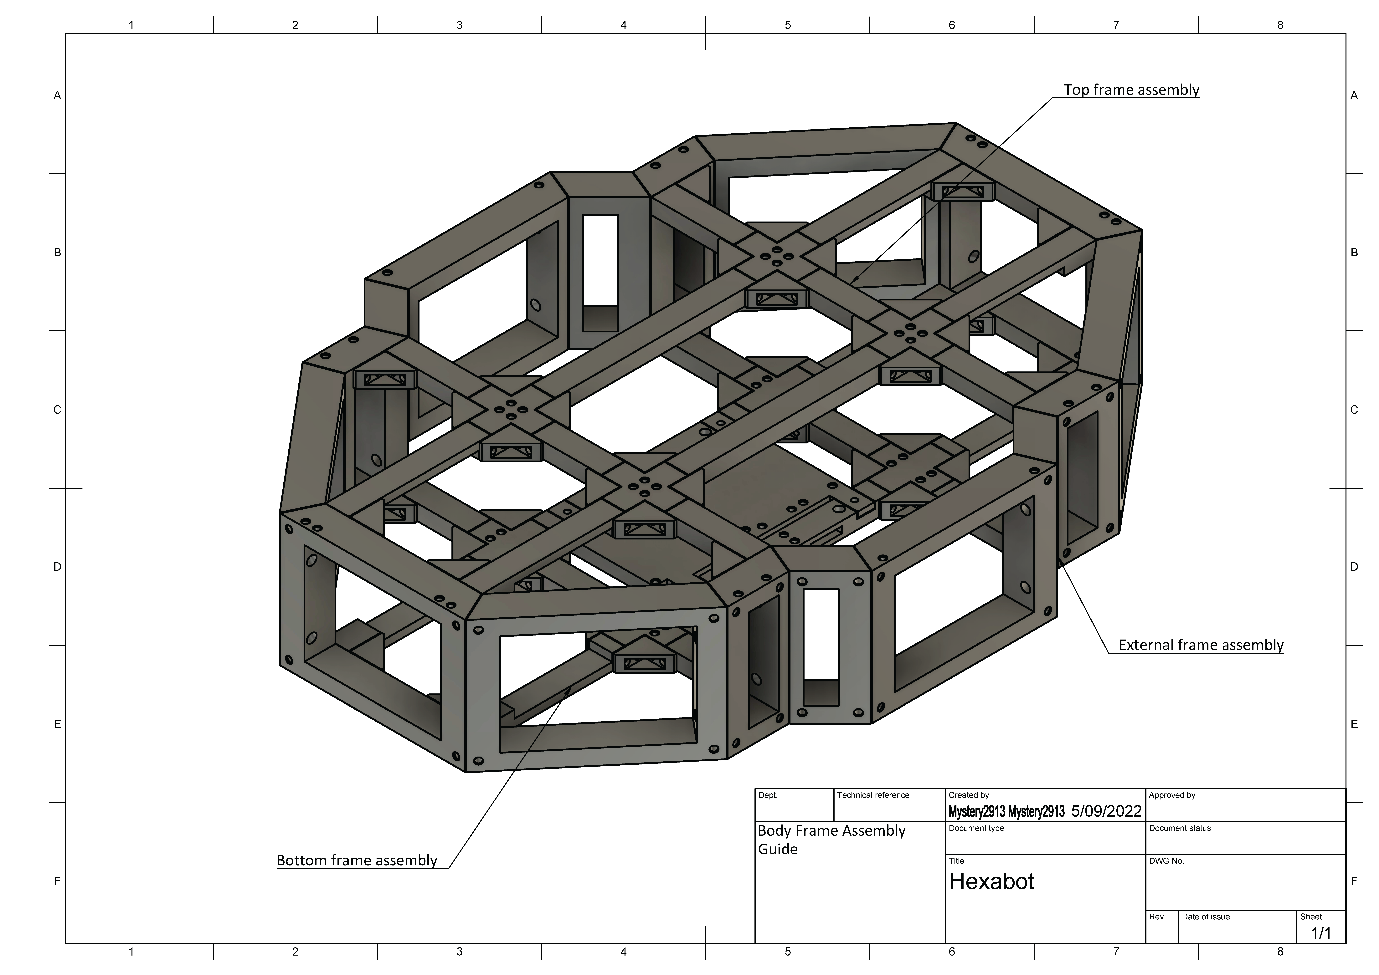
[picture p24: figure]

Figure 7 – 9 Body Frame Assembly

## 10 Leg Assembly

### 10.1 Required parts and tools

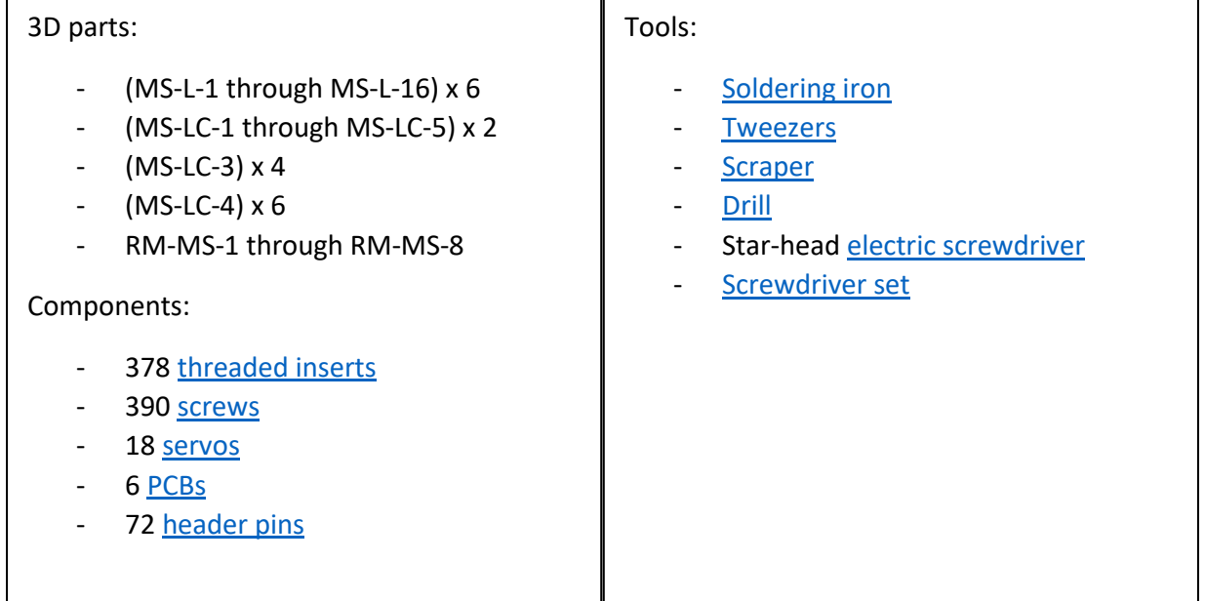
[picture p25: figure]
3D parts:; - (MS-L-1 through MS-L-16) x 6 - (MS-LC-1 through MS-LC-5) x 2 - (MS-LC-3) x 4 - (MS-LC-4) x 6 - RM-MS-1 through RM-MS-8; Components:; - 378 threaded inserts - 390 screws - 18 servos - 6 PCBs - 72 header pins; Tools:; - Soldering iron - Tweezers - Scraper - Drill - Star-head electric screwdriver - Screwdriver set

### 10.2 Preparing parts

The parts MS-L-3, MS-L-8, MS-L-12, MS-L-14 should be printed in green or the chosen highlight colour. Some of these parts need supports to be printed. These should only be used on the prints that absolutely need them. After they have finished printing, the supports can be removed using a scraper. Prepare the rest of the parts as instructed in section 5.2 and 5.3.

### 10.3 Assembly

Follow the steps as instructed below, as well as referring to Figure 8 and Figure 9.

1. Start by taking MS-L-12 and placing a servo motor inside it so that the wire comes out the open side.
2. Screw in the motor at the rear of MS-L-12.
3. Use screws to attach MS-L-13 to MS-L-12 also well as attaching MS-L-13 to the servo motor.
4. Connect MS-L-10, MS-L-11, and MS-L-14 to MS-L-12 using screws.
5. Slot MS-L-6 into the rotational slot in MS-L-10.
6. Refer to section 16 to setup and use the calibration jig.
7. After calibration is complete, take the servo arm and place it onto the motor axle. This is done by placing the assembled leg so far on to Figure 9 and aligning the motor arm so that it is parallel to the next section of the arm. Use a screw to attach the motor arm to the next section of the leg.

8. Slot MS-L-7 into the rotational slot in MS-L-11.
9. Repeat step 1 and 2 but using MS-L-8 instead.
10. Use screws to attach MS-L-9 to MS-L-8 as well as attaching MS-L-9 to the servo motor.
11. Connect MS-L-6 and MS-L-7 to MS-L-8 using screws.
12. Slot MS-L-4 into the rotational slot in MS-L-6.
13. Refer to section 16 to use and setup calibration jig.
14. Repeat step 7 using current servo motor.
15. Slot MS-L-5 into the rotational slot in MS-L-7.
16. Connect MS-L-1, MS-L-2, and MS-L-3 to MS-L-4 and MS-L-5 using screws. Keep the screws that attach to MS-L-2 loose so there is play in that part.
17. Repeat step 1 and 2 but using MC-LC-2 (or its equivalent using the robot main parts) instead.
18. Use screws to attach MC-LC-3 to MS-LC-2 also well as attaching MS-LC-3 to the servo motor.
19. Connect MC-LC-1 to MC-LC-2 using MC-LC-4 and MC-LC-5.
20. Slot MS-L-1 into the rotational slot in MS-LC-1.
21. Refer to section 16 to use and setup calibration jig.
22. Repeat step 7 using current servo motor.

After the leg has been assembled, the PCBs need to be attached to the back of the leg:

1. To prepare the PCB, solder the header pins into each of the 4 pin attachment points on the PCBs. The header pins will need to be split into 3 pin sections.
2. Using screws and the screws holes at the bottom of the PCBs, attach the PCB to the back of the third servo motors housing.

Repeat these processes 6 times so that 6 legs are assembled with PCBs attached. The section with the 3rd servo motor attached will use parts from robot main for 4 out of 6 of the legs.

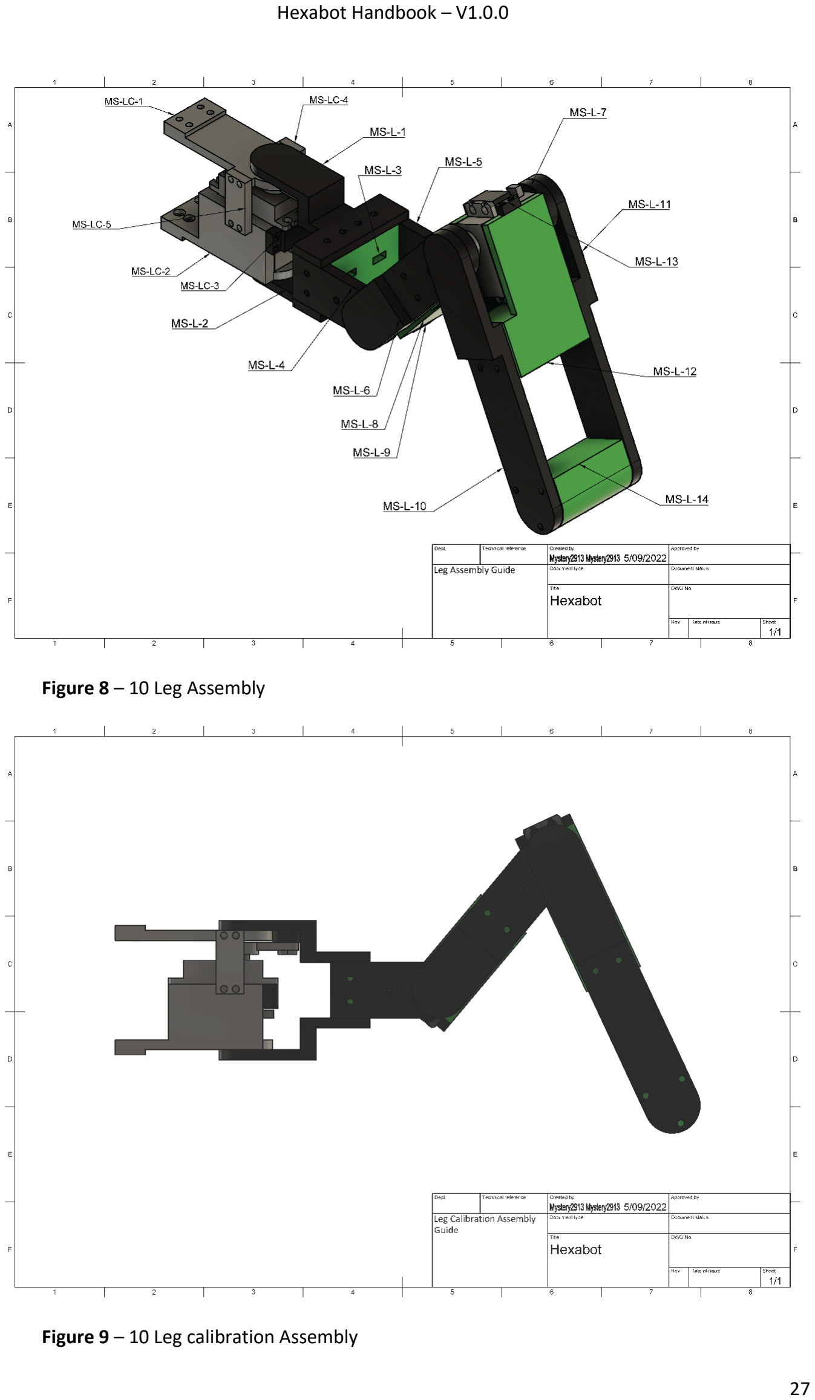
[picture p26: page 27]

Figure 8 – 10 Leg Assembly

Figure 9 – 10 Leg calibration Assembly

## 11 Battery Frame Assembly

### 11.1 Required parts and tools

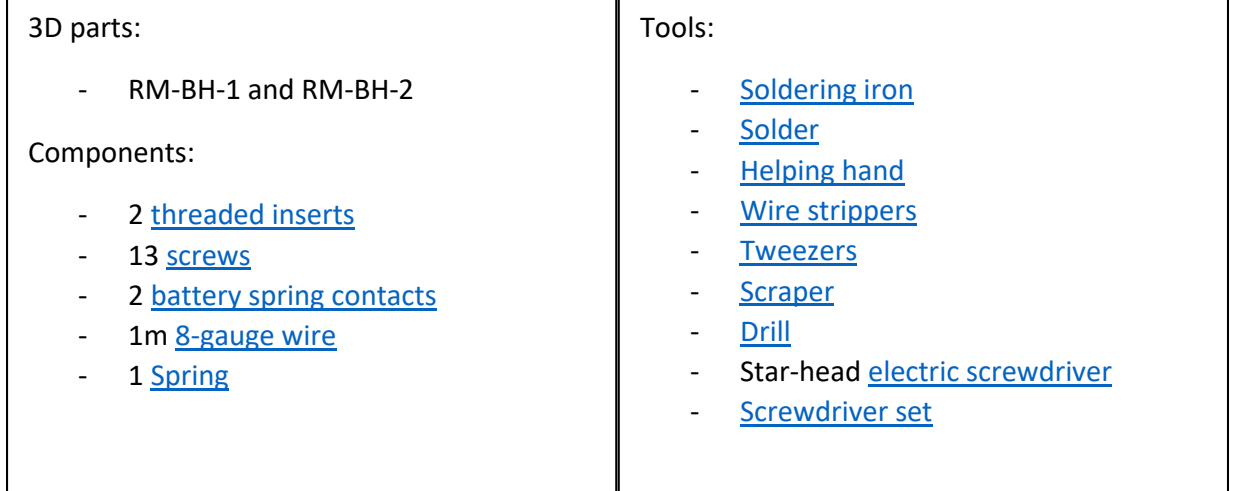
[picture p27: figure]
3D parts:; - RM-BH-1 and RM-BH-2; Components:; - 2 threaded inserts - 13 screws - 2 battery spring contacts - 1m 8-gauge wire - 1 Spring; Tools:; - Soldering iron - Solder - Helping hand - Wire strippers - Tweezers - Scraper - Drill - Star-head electric screwdriver - Screwdriver set

### 11.2 Preparing parts

Prepare parts as instructed in section 5.2 and 5.3. In RM-BH-2, there are screw holes that have openings for the heads to be ‘submerged’ in the plastic. Because of this there are some holes that may need to be widened with a larger drill bit. When doing this, use a 6mm drill bit. RM-BH-1 will need supports while printing. Orienting RM-BH-1 so that the two t-shaped terminals are facing up will give the best result.

### 11.3 Assembly

Before these parts can be attached to the rest of the frame there are some other electronics aspects that need to be completed first.

1. Take the 8-gauge wire and cut 200mm of the red wire off and 100mm of the black wire off.
2. Strip one end of each wire using the wire stripper and tin (put solder on the end) the wires.
3. Solder a wire each to the battery spring contacts on the side where the very small, looped bit of metal is. Use the helping hand to assist.
4. After the battery spring contacts have cooled down, slide the clips on the T-shaped terminals on RM-BH-1 so that that the ends of the spring part of the contacts point towards the front of Hexabot (see Figure 11). Based on Figure 10, the battery spring contact with the red wire should go on the left terminal and the battery spring contact with the black wire should go on the right terminal.

After the battery spring contacts have been prepared, RM-BH-2 needs to have its sprint attached. This can be done by placing the spring in the circular cut in the part in the centre. Then spring can be attached by using the soldering iron to melt the plastic around the base of the spring, stopping it from being unseated (see Figure 11).

Now RM-BH-1 can be attached to the frame as seen in Figure 10. Note that the bottom, front, right brackets has a cut-out for an LED to be placed where one of the screws would sit. Do not put a screw here. After this, RM-BH-2 can be connected to RM-BH-1 with screws.

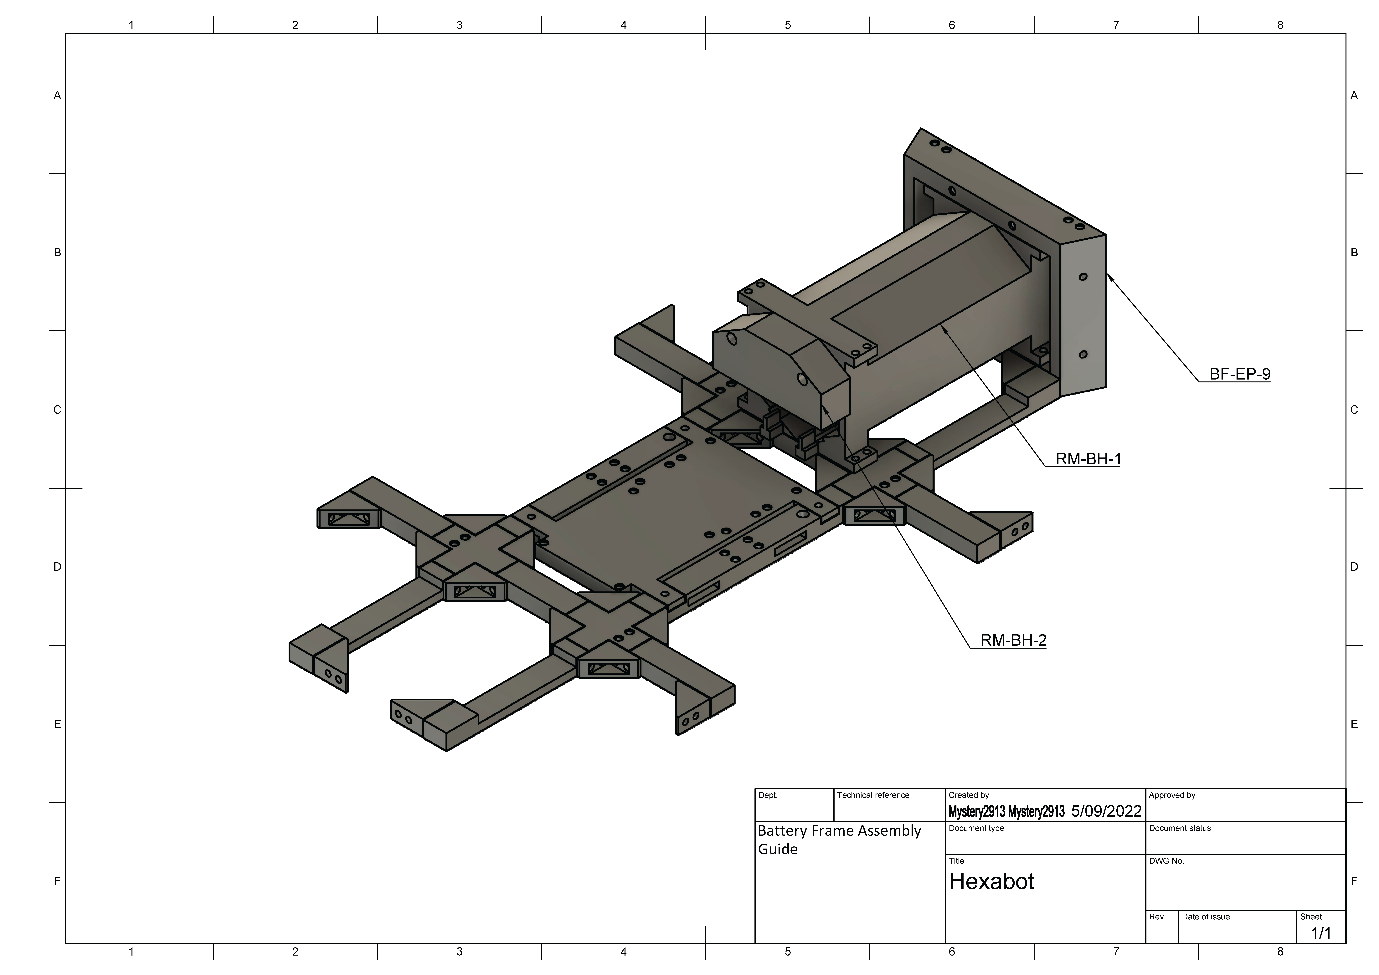
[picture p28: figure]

Figure 10 – 11 Battery Frame Assembly. (Note that the top frame has been removed from this diagram for ease of use, however the RM-BH-1 should be attached to the top frame.)

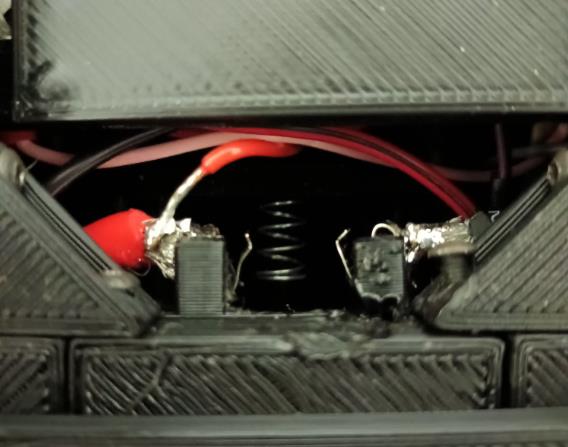
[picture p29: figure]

## 12 Battery Housing Assembly

### 12.1 Required parts and tools

Figure 11

This picture is taken from underneath Hexabot, the bottom of the image is towards the back of Hexabot. The spring and its orientation can be seen in the middle of the image.

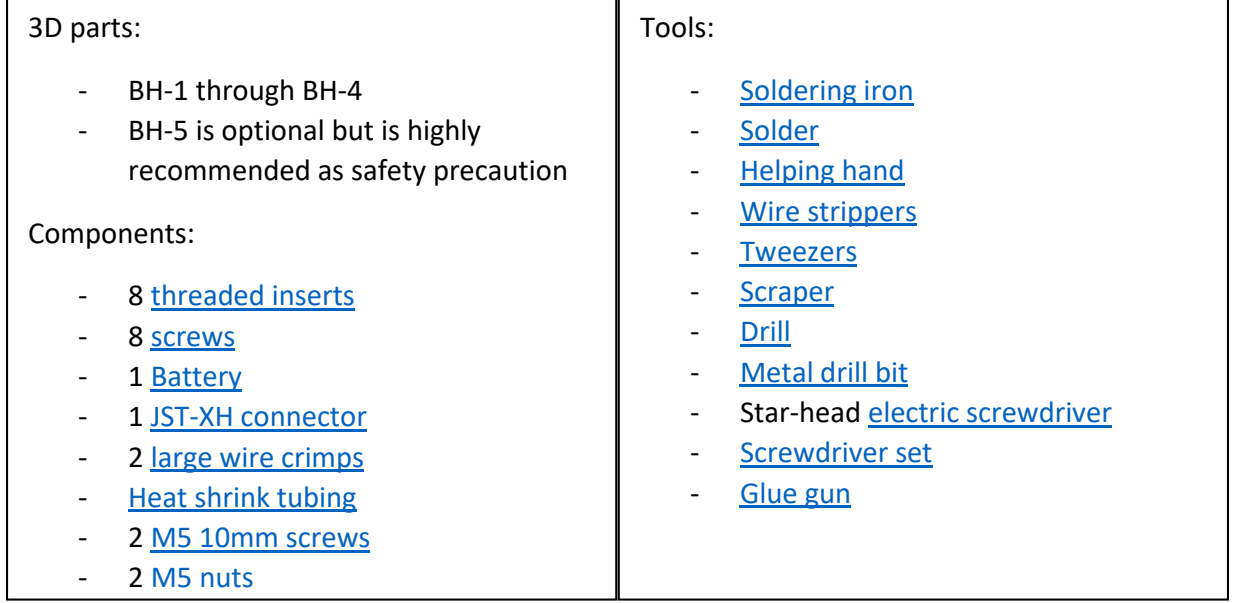
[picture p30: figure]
3D parts:; - BH-1 through BH-4 - BH-5 is optional but is highly recommended as safety precaution; Components:; - 8 threaded inserts - 8 screws - 1 Battery - 1 JST-XH connector - 2 large wire crimps - Heat shrink tubing - 2 M5 10mm screws - 2 M5 nuts; Tools:; - Soldering iron - Solder - Helping hand - Wire strippers - Tweezers - Scraper - Drill - Metal drill bit - Star-head electric screwdriver - Screwdriver set - Glue gun

### 12.2 Preparing parts

Prepare parts as instructed in section 5.2 and 5.3. BH-1 and BH-2 will require supports. This is best done this the point of the part facing up. To prepare the metal plates, use a hacksaw to cut 2 metal plates with the following dimensions: 24mm by 10mm. Then using a metal-rated 5.5mm drill bit, drill a hole 8mm down from the top (along the long edge) on each plate.

### 12.3 Battery safety instructions

During this assembly process, there will be work done around a battery that is charged. Since the use of metal tools is required, be very careful using them around the terminals of the battery because of the risk of a short circuit.

### 12.4 Assembly

First connect BH-1, BH-2, and BH-3 using screws. Once this is done, the insertion of the electronics can start. Refer to Figure 13 during this process.

1. Slide the battery into the housing with the wires at the top.
2. Cross the power wires over and pull them down so they are positioned near the slots for the metal plates. It is useful to place the plates temporarily in their positions so that they can guide where the wire will go.
3. Mark the length that power wires need to be to reach that point and cut them there.
4. Take the large wire crimps temporarily on the ends of the power wires so that you can see at what angle they will need to be positioned at so you can solder them there later.
5. Pull the battery out and take off the power wires.
6. Strip the ends of the power wires and tin them.
7. Slide heat shrink tubing over each wire away from the solder joint.
8. Solder the large wire crimps onto the power wires, matching the colours of the wires and crimps and matching the angle that was found in step 4.
9. Use the ambient heat from the soldering iron or a lighter to shrink the tubing over the exposed solder joint.
10. Replace the wires onto the battery and the battery into the housing.
11. Re-cross the wires and position them, next to the metal plates.
12. Take the power screws and bolts and place slot them through the wire crimps and plates and bolt them tight.
13. Making sure that they are not touching, position the plates as shown in Figure 12 and Figure
13. Use hot glue to lock them in place.

Now that the power from the battery is attached, the balance charging port needs to be transferred.

1. Place a male JST-XH connector and place it into the hole in BH-4. Place it so that the open slots are orientated upwards, and that the exposed pines go into the housing.

2. Cut the existing JST-XH connector from the battery. WARNING. Cut each wire individually, since if multiple wires are cut at once, a short circuit will occur.
3. Strip each wire and tin the end. This process will be slightly difficult since the wires will be connected to the battery.
4. Slide heat shrink tubing over each wire away from the solder joint.
5. Solder the wires to the JST-XH connector’s pins and make sure to keep the wire in the correct order with respect to the original configuration.
6. Use the ambient heat from the solder iron or a lighter to shrink the tubing over the exposed solder joint.
7. Connect BH-4 to the rest of the housing and squish down the wires to that BH-4 fits overtop.
8. Using the glue gun, put a spot of glue between the metal plates on the outside of the housing to add more support to them.

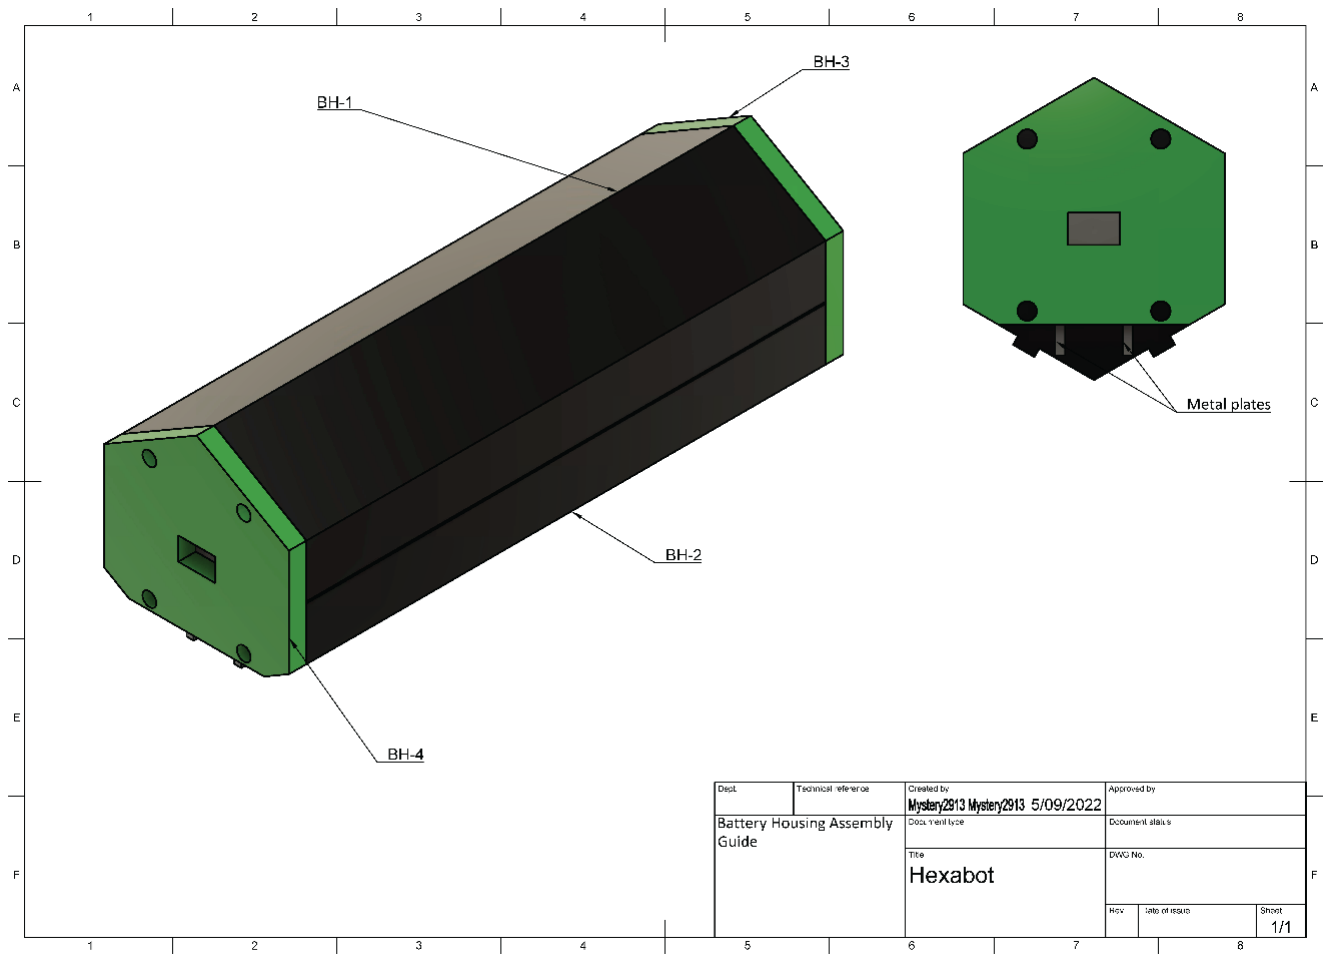
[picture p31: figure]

Figure 12 – 12 Battery Housing Assembly

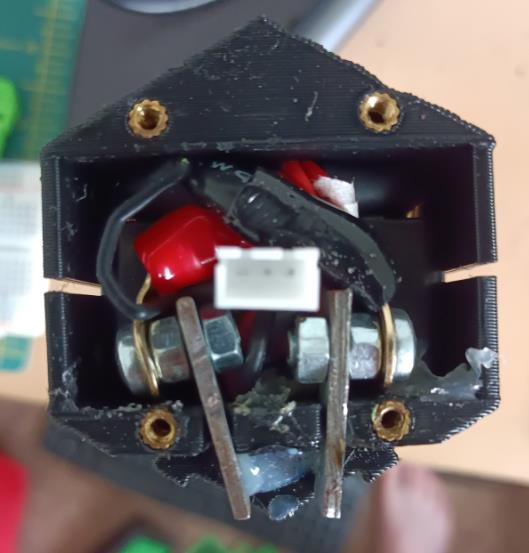
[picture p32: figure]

## 13 Leg Connection Assembly

### 13.1 Required parts and tools

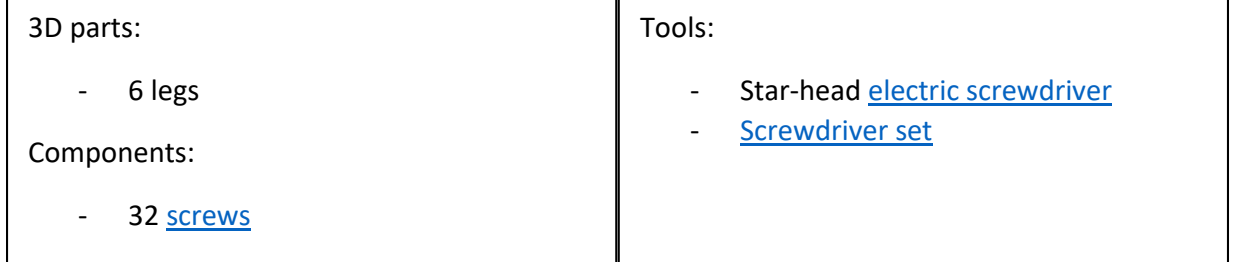
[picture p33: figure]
3D parts:; - 6 legs; Components:; - 32 screws; Tools:; - Star-head electric screwdriver - Screwdriver set

### 13.2 Preparing parts

Place each leg in its corresponding place. Depending on which parts the 3rd section of leg was made of, either robot main or leg connector.

### 13.3 Assembly

To connect the legs to the body frame, some of the legs may need to be partly dismantled to get them in the right positions. It is also recommended to remove the top frame while trying to get the legs in place, as it will make it easier to install them. The top frame can them be reinstalled later while attaching the screws to it. When installing the rear to legs, one of the connecting bars between

Figure 13

12 Battery Housing Assembly, internal battery wiring.

RM-MS-1 and RM-MS-2 as well as RM-MS-3 and RM-MS-4 will not fit because of the battery frame. Because of this remove the connecting bar that is getting in the way.

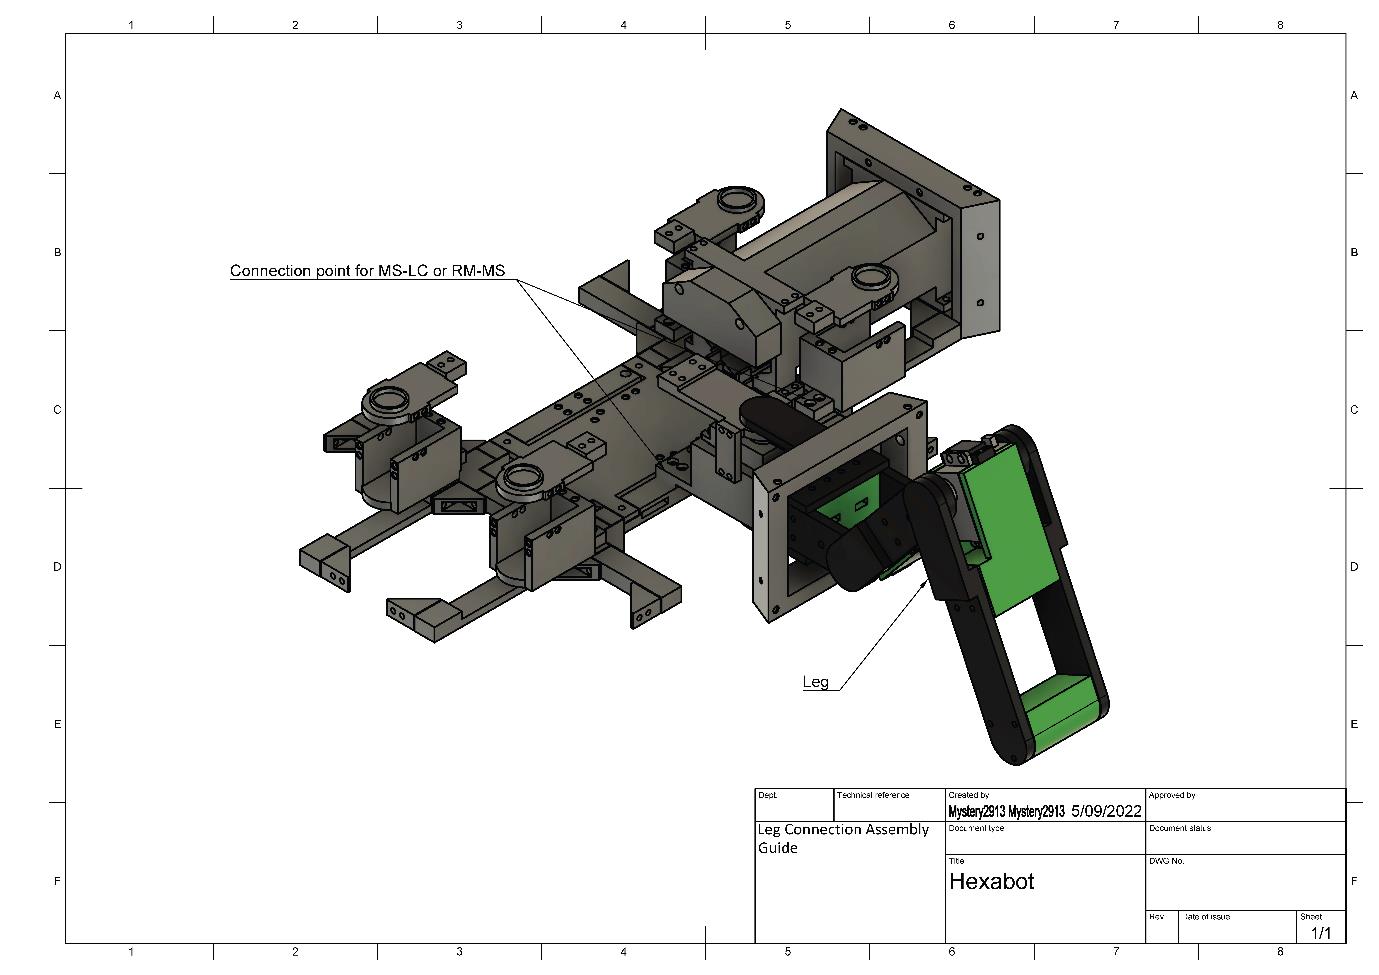
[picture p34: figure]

Figure 14 – 13 Leg Connection Assembly. For the sake of simplicity, there is only one leg, however each leg is used and positioned based on whether it use MS-LC or MS-RM.

## 14 Electronics Assembly

### 14.1 Required parts and tools

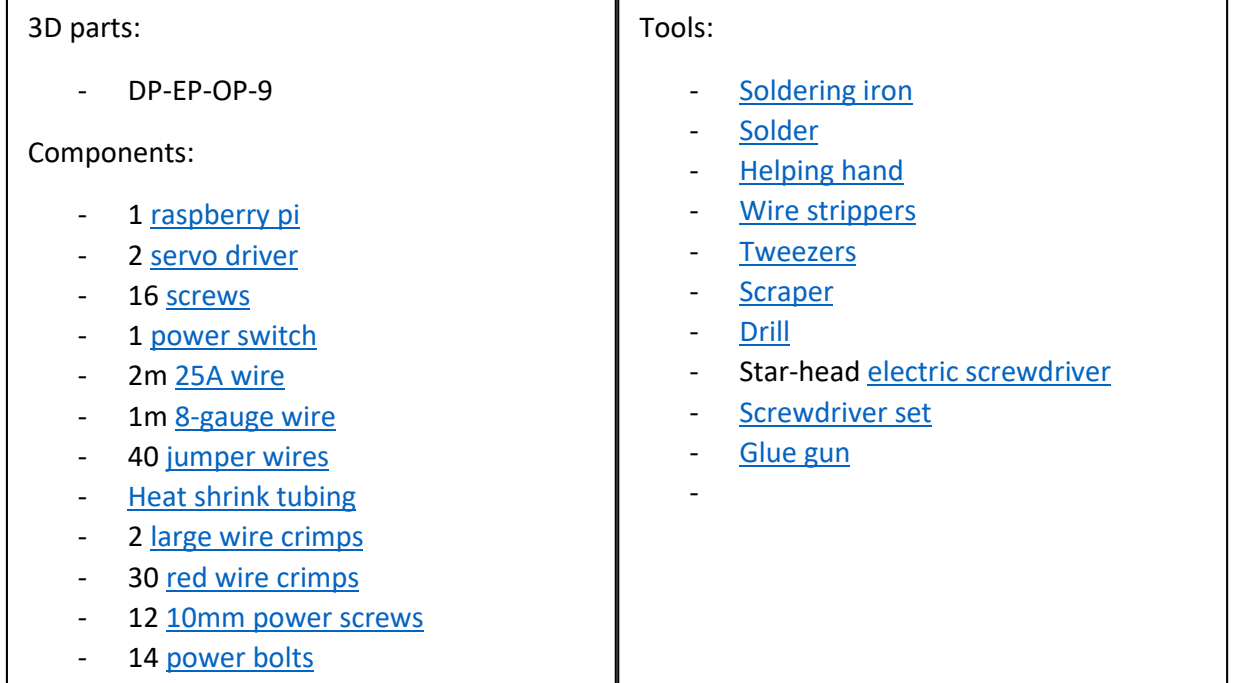
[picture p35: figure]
3D parts:; Components:; - 1 raspberry pi - 2 servo driver - 16 screws - 1 power switch - 2m 25A wire - 1m 8-gauge wire - 40 jumper wires - Heat shrink tubing - 2 large wire crimps - 30 red wire crimps - 12 10mm power screws - 14 power bolts; Tools:; - Soldering iron - Solder - Helping hand - Wire strippers - Tweezers - Scraper - Drill - Star-head electric screwdriver - Screwdriver set - Glue gun -

### 14.2 Preparing parts

To prepare the servo motor drivers, solder the header pins that are supplied onto the boards.

### 14.3 Assembly

The first step is to attach the switch to the back panel.

1. Screw DP-EP-OP-9 to the back of the frame where the battery housing is.
2. Place the power switch in the slot such that the dot on the switch is oriented towards the battery slot.
3. Put a heat shrink tube over red wire that is already attached to the battery frame terminal.
4. Solder the red wire to one of the switch terminals and use heat to shrink the tubing over the solder joint.
5. Get a new section of red 8-gauge wire that is the length of the power screw terminal closest to the switch, to the switch.
6. Strip the wire on both ends.
7. Crimp a large red wire crimp to it and place a heat shrink tube on the wire.
8. Solder the other end of the wire to the switch and shrink the tube over the solder joint.
9. Put the wire crimp onto the power screw.

10. Take the black wire that is already soldered onto the battery frame terminal and crimp a large black wire crimp to it.
11. Place it on the closest power screw.

Next is to assemble and install the power indicator circuit.

1. Using all components specified in the parts list for the power indicator circuit, assemble the circuit by following the power indicator wiring diagram (see Figure 16). To do this, follow this tutorial on how to solder circuits on perfboard: https://www.instructables.com/Using-Perfboard/. (https://www.instructables.com/Using-Perfboard/) The breakout wires VCC, and GND should have wire crimps on them. The V+ wire should be soldered directly to the positive battery frame terminal wire as seen in Figure

### 11. VCC should be attached to the positive power screw and GND should be attached to the

negative power screw.
2. Take the RGB LED and trim their leads and solder wires to them. The blue lead can be completely removed as it is not used. Use heat shrink tubing on each lead to isolate them from each other.
3. Place the RGB LED through the slot for it in the rear of Hexabot. This is positioned on the bracket of the battery frame. Use the glue gun to secure it in place.
4. The other ends of the wires can be attached to their respective header pins on the indicator circuit.

The next step is to attach the motors to the PCBs.

1. Each servo motor needs to connect to the PCBs. The yellow wire is PWM, the red wire is V+, and the brown wire is GND.
2. Servo motor 1 (the first motor that is attached in 10 Leg Assembly) is connected to SRV1.
3. Servo motor 2 (second motor in 10 Leg Assembly) is connected to SRV2.
4. Servo motor 3 (third motor in 10 Leg Assembly) is connected to SRV3.
5. Repeat this for all legs.

Next the boards need to be attached to the electronics plate.

1. Screw the raspberry pi and the servo drivers onto BF-IF-BF-EM-1
2. Using the jumper wires, connect the signal connections (PWM1, PWM2, and PWM3 on the PCBs) to the motor driver board by following Figure 15.

Next is connecting the PCBs power to the power screws.

1. On each PCB, place 2 10mm power screws onto the V+ and GND connections.
2. By measuring out the length of the wires, use the 25A red and black wires to connect the PCBs to the power screws based on the wiring diagram shown on Figure 15. Red wire crimps should be used to connect the wires together.
3. Tighten the crimps to the PCB by using the power nuts.

Now the servo driver board and the raspberry pi needs to be connected.

1. Using jumper wires, connect the servo driver boards together with the raspberry pi as show in Figure 15.
2. Alter a jumper wire by cutting 1 off one of the plastic connectors, striping the wire, and crimping a red wire crimp to the end.
3. Attach this between the raspberry pi and the negative power screw as shown in Figure 15.
4. Use 2 power bolts to bolt all the crimps on the power screws down.

The last step is to attach the raspberry pi battery pack to the raspberry pi using the corresponding cable. Then place the battery back in the front of Hexabot.

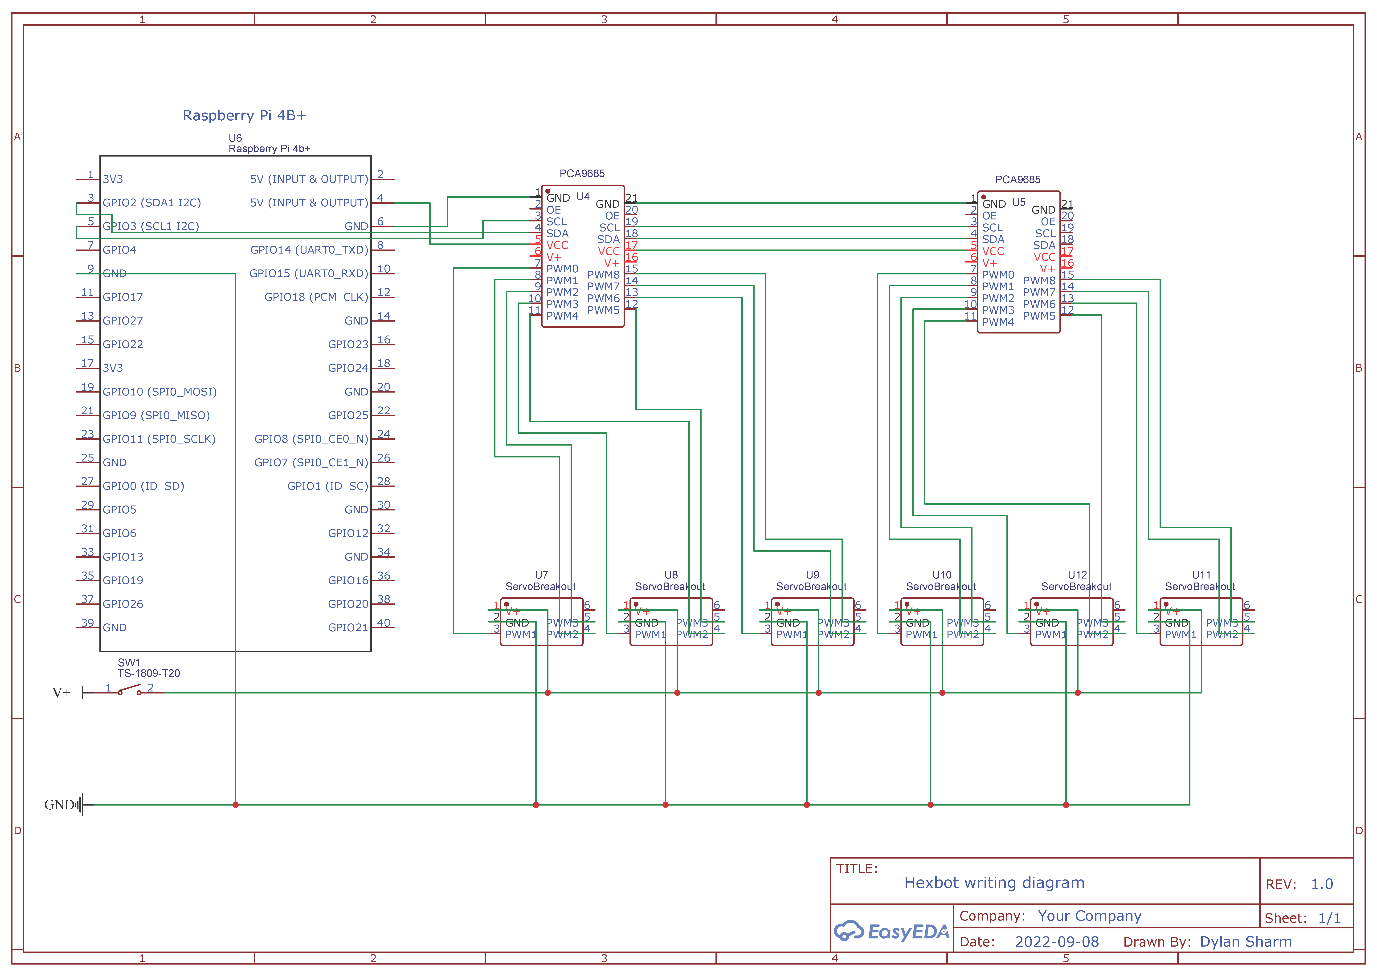
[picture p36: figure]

Figure 15 – 14 Electronics Assembly, Electronics Wiring Diagram

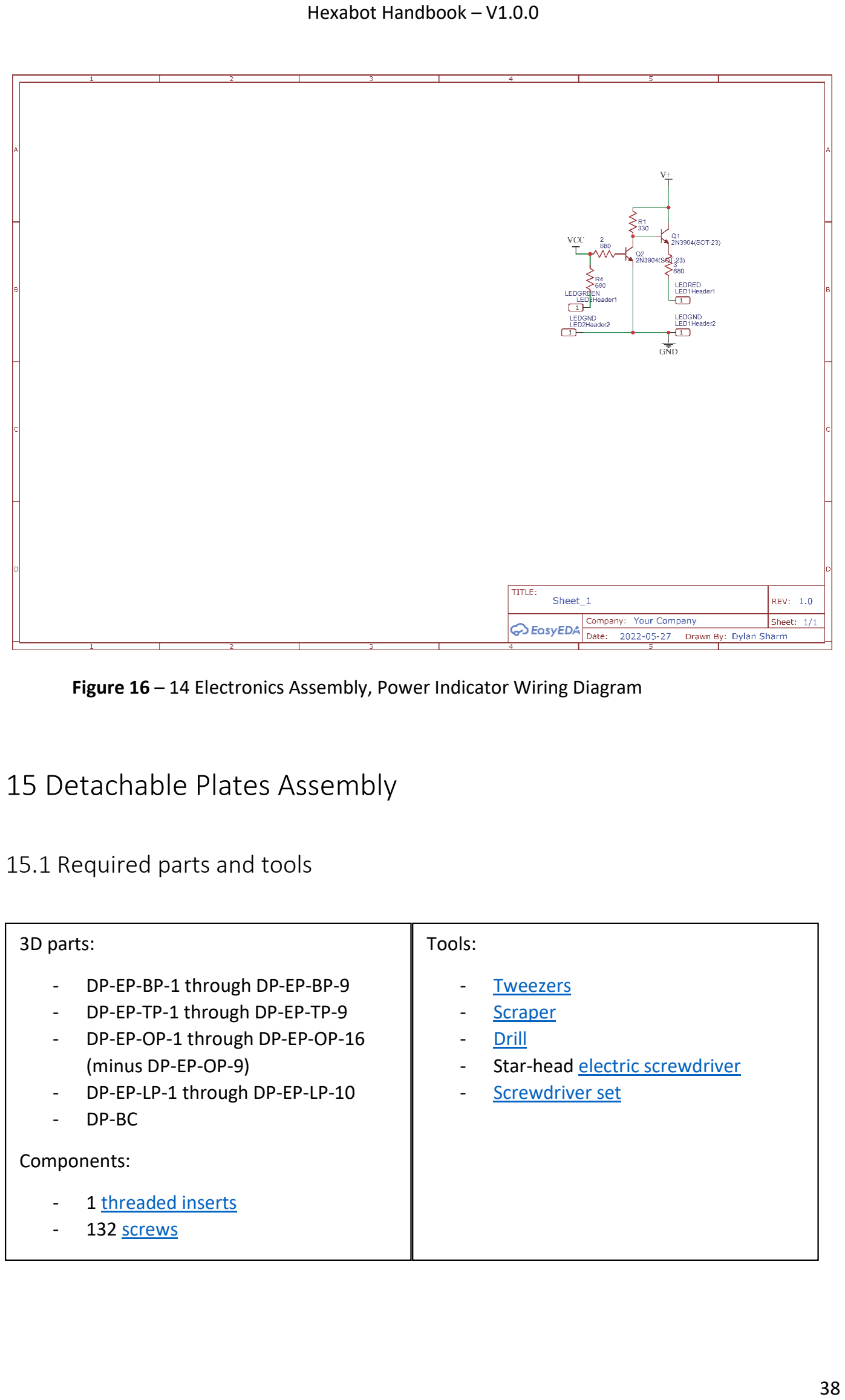
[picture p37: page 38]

Figure 16 – 14 Electronics Assembly, Power Indicator Wiring Diagram

## 15 Detachable Plates Assembly

### 15.1 Required parts and tools

3D parts:

- DP-EP-BP-1 through DP-EP-BP-9
- DP-EP-TP-1 through DP-EP-TP-9
- DP-EP-OP-1 through DP-EP-OP-16 (minus DP-EP-OP-9)
- DP-EP-LP-1 through DP-EP-LP-10
- DP-BC

Components:

- 1 threaded inserts
- 132 screws

Tools:

- Tweezers
- Scraper
- Drill
- Star-head electric screwdriver
- Screwdriver set

### 15.2 Preparing parts

Prepare parts as instructed in section 5.2 and 5.3. All of DP-EP-LP should be printed green or the chosen highlight colour.

### 15.3 Assembly

To assemble, attach all plates to the body frame as shown in Figure 17. DP-BC can be attached onto the threaded insert in DP-EP-OP-9.

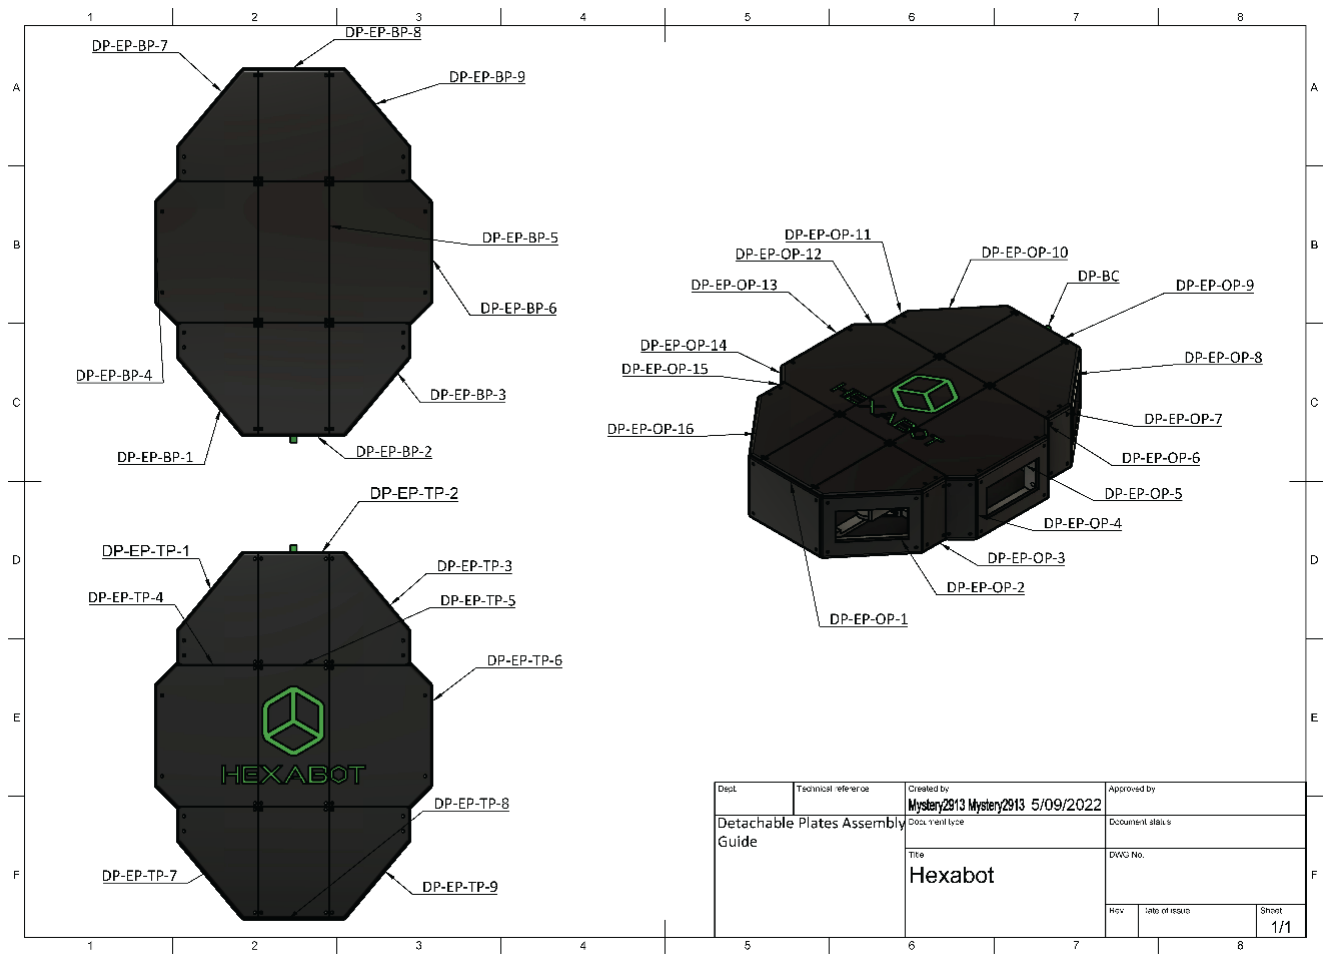
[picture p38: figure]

Figure 17 – 15 Detachable Plates Assembly

## 16 Software setup

### 16.1 Install raspberry pi OS and booting

To install raspberry pi OS follow this guide by Tom’s Hardware: https://www.tomshardware.com/reviews/raspberry-pi-headless-setup-how-to,6028.html

Next turn on raspberry pi by plugging it in to power. After about 30s for it to boot, open a command prompt or terminal on your computer and type:

- ssh pi@raspberrypi

When prompted, type in the password that you set as the user password when you installed the OS. If successful, you should be greeted with a terminal from the raspberry pi.

### 16.2 Setup raspberry pi

There are multiple other settings that need to be enabled on the raspberry pi. If these steps are being done for the calibration of the legs, stop at step 7 and proceed to section 16.3:

1. Enable I2C by typing:
- sudo raspi-config

Use arrow keys and the enter button to navigate to and enable > Interface Options > I2C

2. Install git onto system:
- sudo apt update
- sudo apt install git
3. Verify the installation. Should return lasted version (2.32.0):
- git –version
4. Then after installation and configuration, navigate to Projects in users:
- cd Projects
5. Clone repository:
- git clone https://github.com/Mystery2913/Hexabot.git
6. Navigate into repo:
- cd Hexabot
7. Install dependencies:
- pip install -r requirements.txt
8. Start-up Control site:
- flask run --no-debugger --host=0.0.0.0
9. Use addresses printed in console to connect to website and add /joy to address to access control panel. E.g. 192.168.20.115:5000/joy

### 16.3 Leg calibration

Connect the motor, servo driver, and raspberry pi together by following the wire diagram Figure 18. The flags V+ and GND are the connections to the battery, they can be connected to the rest of the electronics with alligator clips. Depending on which motor you are calibrating, connect the motor to the corresponding PWM slot. First servo motor goes to motor channel 0, seconds servo motor goes to motor channel 1, and third servo motor goes to motor channel 2. Once this is done return to the SSH terminal and type:

- python calibrate.py

Then continue on with steps from section 10.

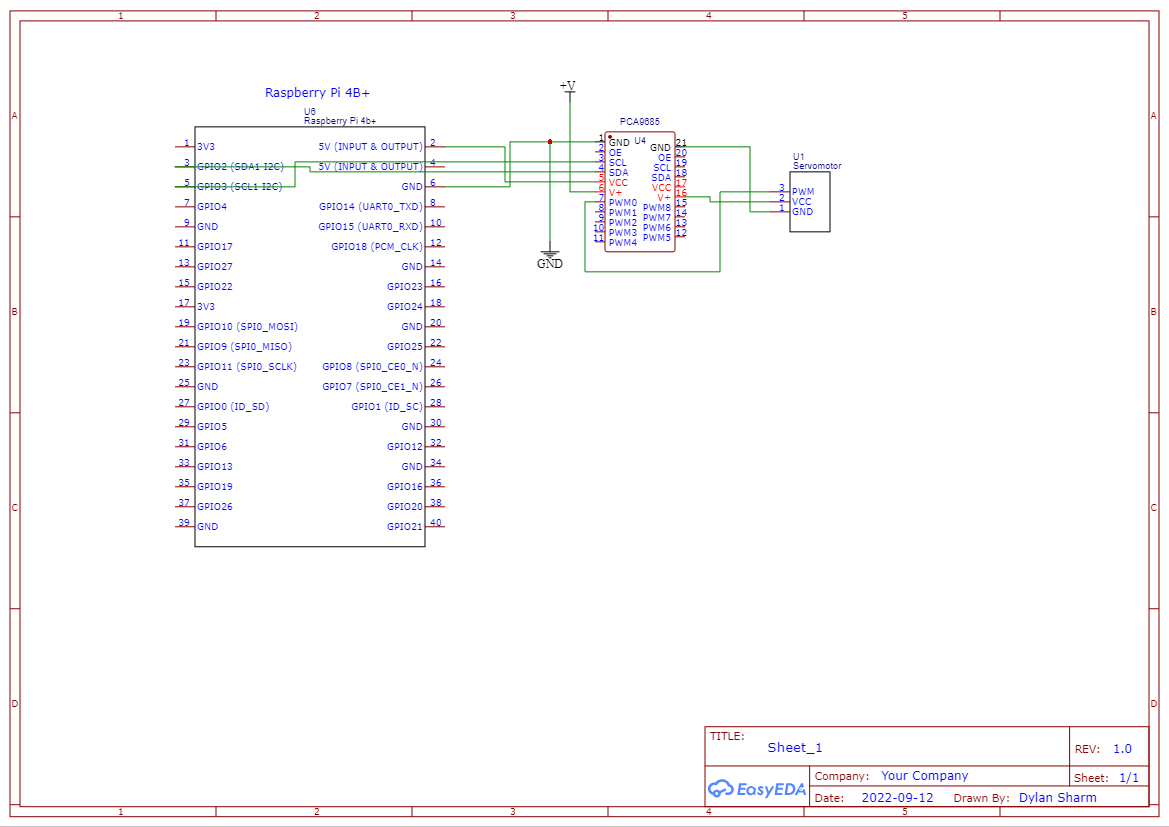
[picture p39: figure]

Figure 18 – 16 Leg calibration wiring diagram

## 17 Acknowledgments

### 17.1 Thank you

Thank you for downloading this user manual in the hope of making Hexabot. I have put a lot of time into this creation, and I am extremely proud of what I have made.

### 17.2 Front cover background

Credit to the maker of the background of the front cover: Алексей Безродний. Thank you for the free license of this image.

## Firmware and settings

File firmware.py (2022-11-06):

"""
GNU General Public License v3.0 (GPL-3.0)

This file is part of the Hexabot Project (https://github.com/Mystery2913/Hexabot).
Copyright (C) 2022 Dylan Sharm (Mystery2913).

Copyright (C) 2007 Free Software Foundation, Inc. https://fsf.org/
Everyone is permitted to copy and distribute verbatim copies of this license document, but changing it is not allowed.

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
import math
import time
from board import SCL, SDA
import busio
from adafruit_motor import servo
from adafruit_pca9685 import PCA9685

class Hexabot:
    """
    A class to control Hexabot robot
    ================================
    * Author: Dylan Sharm

    ...

    Args:
        None

    Returns:
        None

    Methods
    -------
    `walkForward`(speed) -> None
        Moves Hexabot forward by 1 step of 3 steps in cycle

    `walkForwardSlow`(speed) -> None
        Moves Hexabot forward by 1 step of 6 steps in cycle
    
    `disableMotors`() -> None
        Disables all motors, will only stop motors from holding position if power is cycled

    """

    def __init__(self) -> None:
        # Initialise busIO by linking to I²C bus lines and initialise the 2 PCA9685 chips with 50Hz PWM frequency.
        self.i2c = busio.I2C(SCL, SDA)
        # pca0 is the first servo driver with the address of 64 (0x40) and pca1 is the second servo driver with the address of 65 (0x41) and has its A0 solder pads bridged.
        self.pca0 = PCA9685(self.i2c, address=64)
        self.pca1 = PCA9685(self.i2c, address=65)
        self.pca0.frequency = 50
        self.pca1.frequency = 50
        # updateRate is a value for the time in seconds it takes to execute an interpolation sequence frame. It can be adjusted here to tune the accuracy of the duration of each movement.
        self.updateRate = 0.1
        self.pcaSet = [self.pca0, self.pca1]
        # Initialise each leg with its corresponding indexes.
        self.leg0 = Leg(0, self.pcaSet, self.updateRate)
        self.leg1 = Leg(1, self.pcaSet, self.updateRate)
        self.leg2 = Leg(2, self.pcaSet, self.updateRate)
        self.leg3 = Leg(3, self.pcaSet, self.updateRate)
        self.leg4 = Leg(4, self.pcaSet, self.updateRate)
        self.leg5 = Leg(5, self.pcaSet, self.updateRate)
        self.legs = [self.leg0, self.leg1, self.leg2, self.leg3, self.leg4, self.leg5]
        # slowWalkingIndexList defines the sequence of the walkForwardSlow() method, and slowWalkingIndexNum stores the leg to be moved.
        self.slowWalkingIndexList = [2, 3, 1, 4, 0, 5]
        self.slowWalkingIndexNum = 0

    def walkForward(self, speed: float) -> None:
        """
        Moves Hexabot forward by 1 step of 3 steps in cycle.
        
        Cycles each leg through 3 coordinate states over a period of time defined by `speed`.
        Each execution acts as one step, and the walking index of each leg is stored in the leg. 

        Args:
            `speed` (float): Defines the speed of the step, is a percentage between 0 - 1.
        
        Returns:
            None
        """
        # Each set of coordinates corresponds to the positions of 3 points in the walking sequence. Index 2 of these lists are angles not Z coords.
        forwardUpCoord = [-20, 10, 15]
        forwardDownCoord = [-80, -120, 15]
        backDownCoord = [-80, -120, -15]
        coords = [forwardUpCoord, forwardDownCoord, backDownCoord]
        # shortestDurationStep specifies the duration of the fastest move and longestDurationStep specifies the duration of the slowest move. Values are in seconds.
        shortestDurationStep = 0.5
        longestDurationStep = 3
        # The `speed` argument is a percentage between 0 and 1, and then is scaled to the shortest and longest duration. E.g. if `speed` was 1, the stepDuration would be 0.5.
        stepDuration = longestDurationStep + (((speed-0)*(shortestDurationStep-longestDurationStep))/(1-0))

        for leg in self.legs:
            # Assign each legs current x and y coords to its own x and y attribute. The position in the sequence of each leg is determined by its walking index.
            leg.x = coords[leg.walkingIndex][0]
            leg.y = coords[leg.walkingIndex][1]
            # The legs that are on the left side of Hexabot (leg index 0-2) need to have their zAngle inverted, since all legs need to be moving in the same direction.
            if math.floor(leg.index/3) == 0:
                leg.zAngle = (coords[leg.walkingIndex][2]) * -1
            else:
                leg.zAngle = (coords[leg.walkingIndex][2])
            # Each legs increment arrays are generated using the assigned coords 
            leg.incrementArray = leg.processLegCoord(leg.x, leg.y, zAngle = leg.zAngle, duration=stepDuration)
        
        # The number of frames in the interpolation sequence is determined by stepDuration / self.updateRate.
        for i in range(int(stepDuration / self.updateRate)):
            # For each interpolation sequence frame move each leg on step along in its sequence. This means that the legs move simultaneously.
            for leg in self.legs:
                leg.moveFrame(leg.incrementArray)

        # After one step shift each legs.
        for leg in self.legs:
            leg.shiftWalkingIndex()
    

    def walkForwardSlow(self, speed: float) -> None:
        """
        Moves Hexabot forward by 1 step of 6 steps in cycle.
        
        Cycles 1 leg at a time through 3 coordinate states over a period of time defined by `speed`.
        Each execution acts as one step, and the current leg this is next leg to move is stored in Hexabot. 

        Args:
            `speed` (float): Defines the speed of the step, is a percentage between 0 - 1.
        
        Returns:
            None
        """
        # Each set of coordinates corresponds to the positions of 3 points in the walking sequence. Index 2 of these lists are angles not Z coords.
        forwardUpCoord = [-20, 10, 15]
        forwardDownCoord = [-80, -120, 15]
        backDownCoord = [-80, -120, -15]
        coords = [forwardUpCoord, forwardDownCoord, backDownCoord]
        # shortestDurationStep specifies the duration of the fastest move and longestDurationStep specifies the duration of the slowest move. Values are in seconds.
        shortestDurationStep = 0.5
        longestDurationStep = 3
        # shortestDurationStep specifies the duration of the fastest pause and longestDurationStep specifies the duration of the slowest pause. Values are in seconds.
        shortestDurationPause = 0.5
        longestDurationPause = 1.5
        
        # The `speed` argument is a percentage between 0 and 1, and then is scaled to the shortest and longest duration. E.g. if `speed` was 1, the stepDuration would be 0.5.
        stepDuration = longestDurationStep + (((speed-0)*(shortestDurationStep-longestDurationStep))/(1-0))
        pauseDuration = (longestDurationPause) + (((speed-0)*((shortestDurationPause)-(longestDurationPause)))/(1-0))
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

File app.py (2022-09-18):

"""
GNU General Public License v3.0 (GPL-3.0)

This file is part of the Hexabot Project (https://github.com/Mystery2913/Hexabot).
Copyright (C) 2022 Dylan Sharm (Mystery2913).

Copyright (C) 2007 Free Software Foundation, Inc. https://fsf.org/
Everyone is permitted to copy and distribute verbatim copies of this license document, but changing it is not allowed.

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
from flask import Flask, render_template, request
import firmware
import multiprocessing as mp
import ctypes

# Initialise the walking and speed shared memory variables and the stackExecute class.
walking = mp.Value(ctypes.c_bool, False)
walkingSlow = mp.Value(ctypes.c_bool, False)
speed = mp.Value(ctypes.c_float, 0)
queue = firmware.stackExecute()

# Initialise the process with the queue method and pass it `walking` and `speed` arguments, then start the process.
process = mp.Process(target=queue.queue, args=(walkingSlow, walking, speed))
process.start()

robot = firmware.Hexabot()

app = Flask(__name__)

@app.route('/', methods=["GET", "POST"])
def index():
    return render_template("index.html")

# Post request for passing data to the backend.
@app.route('/joy', methods=["GET", "POST"])
def data():
    if request.method == "POST":
        # Unpack data
        jsonData = request.get_json()
        print(jsonData)
        # If the data type is normal, then set the walking value to True. This will cause the queue process on call Hexabot.walkForward().
        if jsonData["type"] == "Normal":
            y = int(jsonData['y'])
            if y > 0:
                # Scale the y value of the joystick to the speed passed to stackExecute.queue() and then to Hexabot.walkForward().
                speed.value = y / 100
                walking.value = True
            return {
                'response' : 'I am the response'
            }
        # If the data type is Slow, then set the walkingSlow value to True. This will cause the queue process on call Hexabot.walkForwardSlow().
        elif jsonData["type"] == "Slow":
            y = int(jsonData['y'])
            if y > 0:
                # Scale the y value of the joystick to the speed passed to stackExecute.queue() and then to Hexabot.walkForward().
                speed.value = y / 100
                walkingSlow.value = True
            return {
                'response' : 'I am the response'
            }
        # If the data type is stand, run the moveLeg method to make Hexabot stand.
        elif jsonData["type"] == "stand":
            for leg in robot.legs:
                leg.moveLeg(-80,-120, 0, 0.5)
            return {
                'response' : 'I am the response'
            }
    return render_template('joy.html')

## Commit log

2022-05-15 Worked on the test program for the leg, just did for matting
2022-05-21 Worked on the z axis motion algorythm
    The algorythm is still incorect as it doesnt adjust for the change in the z axis
2022-08-31 Adding all files before dirctory clean up
    Pushing directory in current state as backup
2022-08-31 Changed how the post request sends data, and added feature to reset leg postions on control page
    [app.py, firmware.py]
2022-09-01 Added documentation to firmware.py and app.py
    Added documentation to firmware.py and app.py and fixed the inhertence of updateRate between Hexabot class and Leg class. Added license header to some files. Added icon feature to joy page.
    [app.py, firmware.py]
2022-09-02 Updated README.md and added files
    Updated README.md and added STL files and draft of user manual
    [BF-EP-1.stl, BF-EP-10.stl, BF-EP-11.stl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]
2022-09-05 Uploaded cura printing profile
2022-09-18 Added feature to move slow by moving each leg individually
    Added documentation to match
    [BF-EP-1.stl, BF-EP-10.stl, BF-EP-11.stl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]
2022-11-06 Fixed missing documention and bug in markdown
    Fixed missing documention in firmware.py, fixed bug in README.md link to user manual, and added front cover image to README.md
    [calibrate.py, firmware.py]

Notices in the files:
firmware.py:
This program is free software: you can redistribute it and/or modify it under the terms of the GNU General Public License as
